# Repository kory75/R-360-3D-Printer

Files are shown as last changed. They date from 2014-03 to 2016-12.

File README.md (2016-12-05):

#R-360-3D-Printer

First open source polar RepRap 3d printer

##Documentation

You can find more information and tutorials on the following links:
[Reprap Wiki](http://reprap.org/wiki/R_360)
[replicatorwarehouse.com](http://replicatorwarehouse.com/r-360-modular-printer-with-rotating-bed/)

##BOM

###Plastic Parts

| Quantity | Description |
| --- | --- |
| 1x | Centring Tool |
| 1x | Extruder Holder |
| 1x | Extruder Holder Extension(Dual head only) |
| 1x | Extruder inlet(one is enough, but we recommend to have 3) |
| 1x | Extruder large gear |
| 1x | Extruder small gear |
| 3x | Leveller |
| 1x | X-carriage |
| 1x | X-endstop-holder |
| 1x | X-end |
| 1x | X motor holder |
| 1x | Y-axes large gear |
| 1x | Y-axes small gear |
| 1x | Y-axes support cap |
| 1x | Y base |
| 1x | Y idler |
| 1x | Z-axes base |
| 1x | Z-end top |
| 1x | Z endstop holder |
| 1x | Ramps box Bottom (optional) |
| 1x | Ramps box Top (optional) |
| 1x | LCD box back (optional) |
| 1x | LCD box front (optional) | 

###Laser Cut Parts

| Quantity | Description |
| --- | --- |
| 1x | disc_full-low |
| 1x | dixc_full-top |

###Vitamins

We use allen bolts as as standard. We marked the other types when it is diviates (like Hex Head).

####Rods

| Quantity | Description |
| --- | --- |
| 1x | 200mm M8 threaded rod
| 1x | 250mm M8 threaded rod
| 1x | 280mm M5 threaded rod
| 2x | 320mm M8 smooth rod
| 2x | 380mm M10 smooth rod  

####Bolts and Nuts And Springs

| Quantity | Description |
| --- | --- |
| 8x | M8 Nut |
| 8x | M8 Washer Shake-proof |
| 5x | M8 Washer |
| 1x | M8 Nylock Nut |
| 1x | M8 70mm Hex head Bolt |
| 21x | M3 10mm Bolt |
| 15x | M3 Nuts |
| 4x | M3 Nylock Nuts |
| 18x | M3 Washer |
| 1x | M3 12mm bolt |
| 1x | M3 16mm Bolt |
| 8x | M3 20mm Bolt |
| 3x | M3 30mm Bolt |
| 1x | M3 40mm Bolt |
| 2x | M3 50mm Hex head Bolt |
| 1x | M5 Nut |

#####Extruder Bolts and Nuts

| Quantity | Description |
| --- | --- |
| 1x | M8 Nylock Nut (extruder) |
| 1x | M8 Hobbed Bolt (extruder) |
| 2x | M8 Penny washers (extruder) |
| 4x | M8 Washers (extruder) |
| 2x | M4 50mm Bolt (extruder) |
| 2x | M4 Nut (extruder) |
| 2x | M4 Washer (extruder) |
| 1x | M3 25mm Bolt (extruder) |

####Springs

| Quantity | Description |
| --- | --- |
| 4x | Bed Springs length: 13mm inner diameter: 3.15mm |
| 1x | Extruder Spring (per extruder) length: 15mm inner diameter: 4.2mm |

####Bearings

| Quantity | Description |
| --- | --- |
| 3x | 608zz |
| 3x | 623zz |
| 4x | LM8UU |
| 4x | LM10UU |

####Electronics

| Quantity | Description |
| --- | --- |
| 1x | Ramps 1.4 | 
| 1x | Arduino Mega 2560 |
| 4x | Polulu A4988 (5 for dual setup) |
| 2x | Mechanical Endstops |
| 1x | LCD Screen (optional but strongly recommended) | 
| 1x | Power Supply 12V 5A with 2.5mm round plug and local socket power cable |
| 1x | 2.5mm solderless socket |
| 1x | USB Cable | 
| 2x | 3 wire endstop cable | 
| 4x | 4 wire Motor cables |
| 1x | 2 wire Heater cartridge (per extruder) | 
| 1x | 2 wire Fan (per extruder) | 
| 1x | 2 wire Thermostate Cable (per extruder) | 
| 1x | 2 wire Electronics Cooling Fan | 

####Motors

| Quantity | Description |
| --- | --- |
| 4x | Nema 17 (4.4kg torque) shaft flattened on one side (~1mm) |

####Extruder

ActiveX or ActiveX Dual extruder

####Other

| Quantity | Description |
| --- | --- |
| 20x | Zip ties |
| 1m | Cable organiser 1cm diameter |
| 200mm | Cable organiser 2cm diameter |
| 450mm | GT2 belt |
| 1x | GT2 pulley for 5mm shaft |
| 1x | 5mm to 5mm flexible coupling |
| | 3M blue masking tape |
| 400mm | Heat-shrink inner diameter: 2.5mm |
| 1x | 12V Power Switch | 

##Developers

Kornel Farkas 

Email: admin@replicatorwarehouse.com 

Website: Replicatorwarehouse.com

##Licences

####R-360 Printer 

[R-360 is licenced under CC-BY-SA](http://creativecommons.org/licenses/by-sa/3.0/)

####Greg's Wade Licence

The included and modified extruder parts are based on Greg's Wade extruder.
Greg's Wade Extruder is licensed under the Creative Commons - GNU GPL license. 
2010 by GregFrost
Extruder based on Prusa git repo.
http://www.thingiverse.com/thing:6713

####R-360 Logo

The R-360 logo is not included! Can I have your cool logo on my printer? :) 
R-360 Logo contains our company logo which is trade marked so please do not use unauthorised. However the logo is not required for the functionality of the printer, but it makes it look much cooler! ;) If you like to have the full experience and you would like to have our official logo on your printer :) and you would like to support us to continue to develop the R-360 printer, then please donate 5 USD to us and we will allow you to print and use our logo on your printer. :) Drop us an email to admin@replicatorwarehouse.com

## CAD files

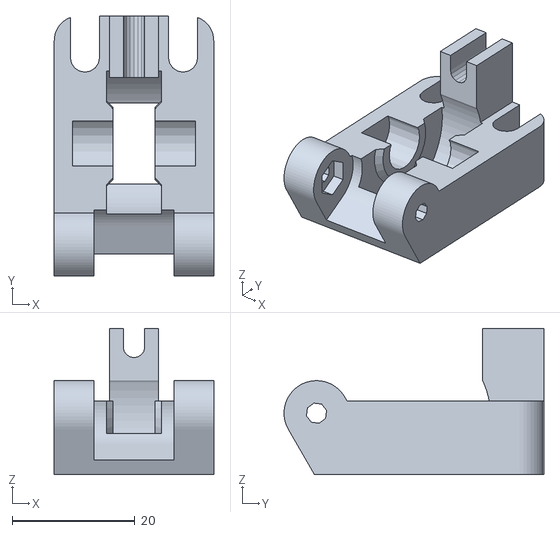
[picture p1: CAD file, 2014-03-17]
extruder/extruder_idler.stl
26.0 x 42.4 x 23.8

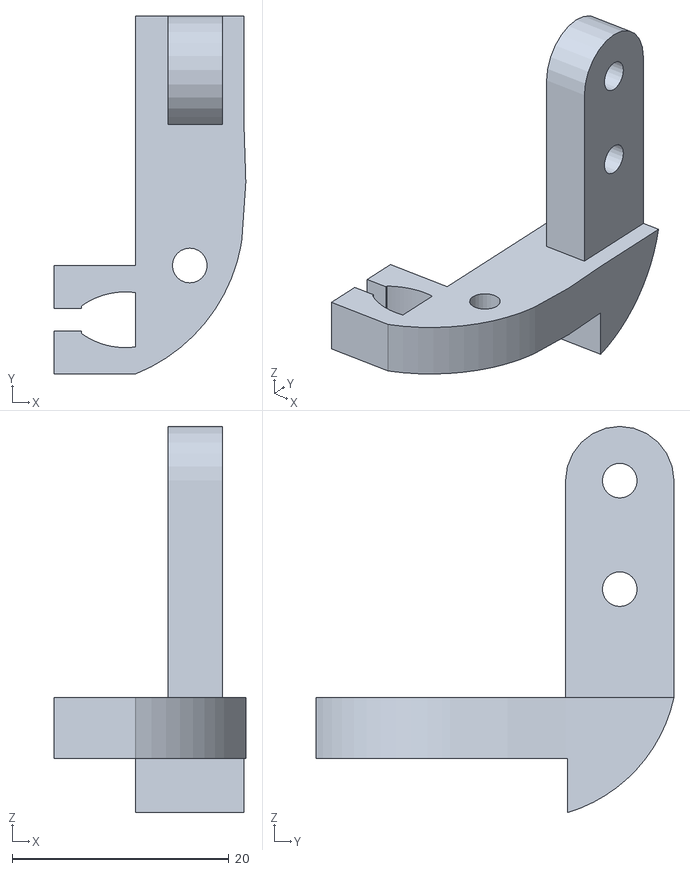
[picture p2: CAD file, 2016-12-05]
X-endstop-holder.stl
17.7 x 33.0 x 35.6

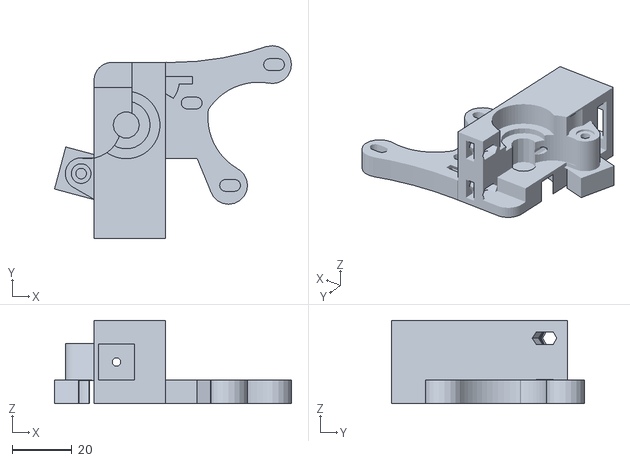
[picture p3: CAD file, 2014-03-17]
extruder/extruder body.stl
79.5 x 64.6 x 28.0

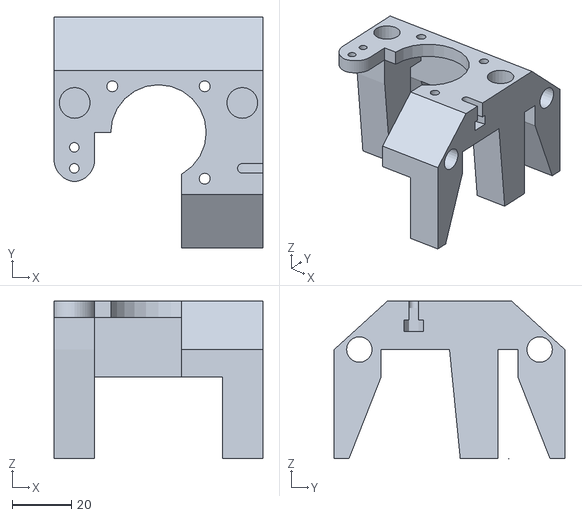
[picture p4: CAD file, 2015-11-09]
Z-axes base.stl
70.6 x 77.9 x 53.3

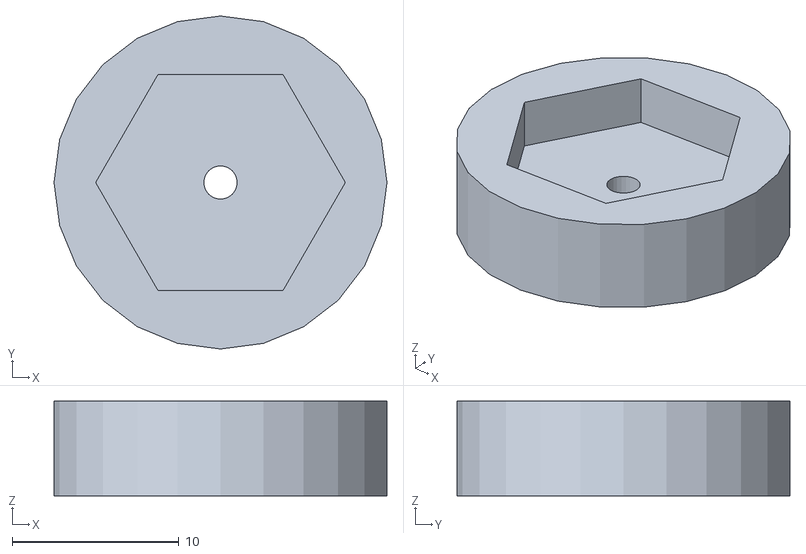
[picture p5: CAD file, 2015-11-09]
Y-axes Support cap.stl
20.0 x 20.0 x 5.70

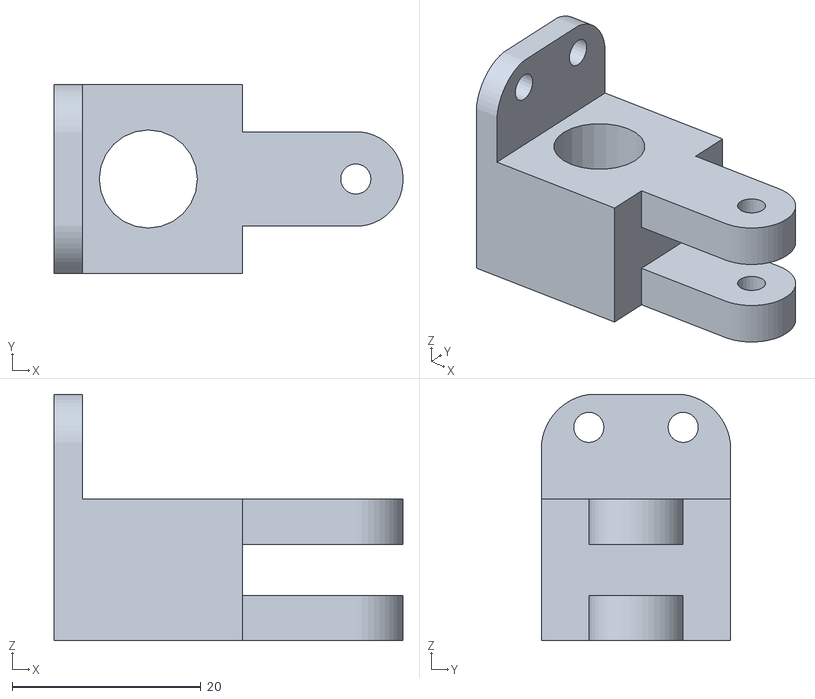
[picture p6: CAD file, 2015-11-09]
Z-endstop holder.stl
37.0 x 20.0 x 26.1

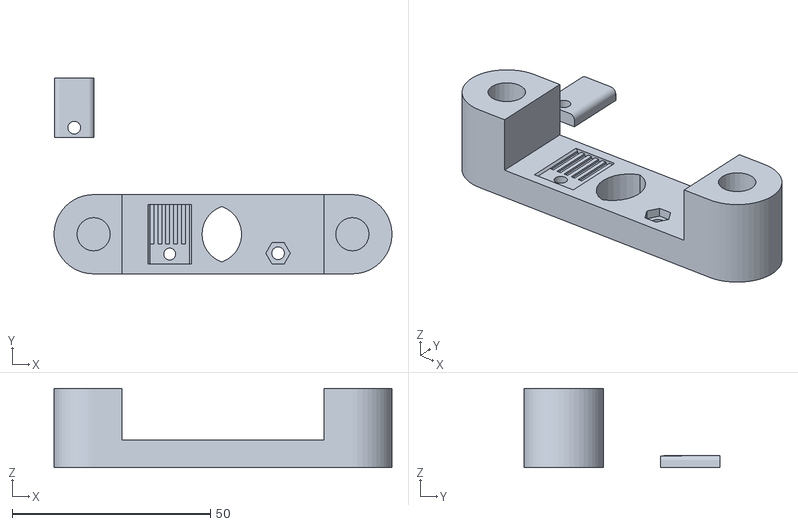
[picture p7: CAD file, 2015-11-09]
X-end.stl
85.3 x 49.4 x 20.0

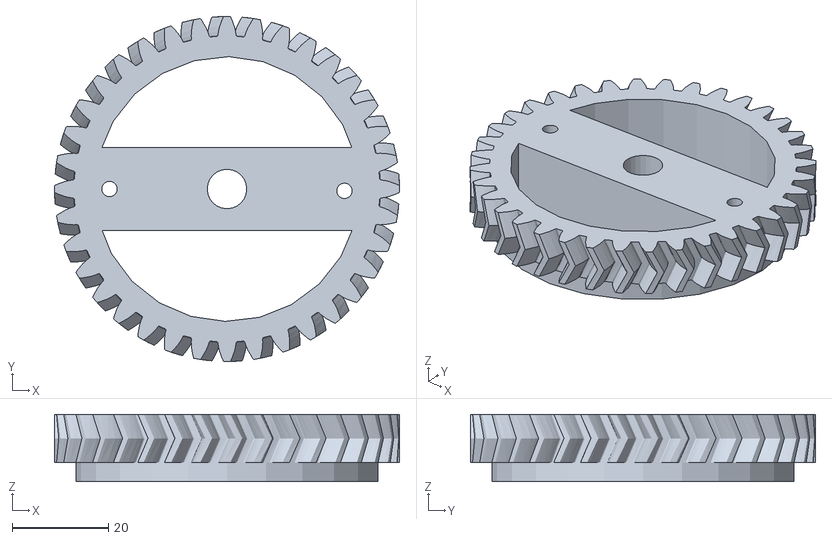
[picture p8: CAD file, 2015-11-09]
Y-axes large gear.stl
71.7 x 71.7 x 14.0

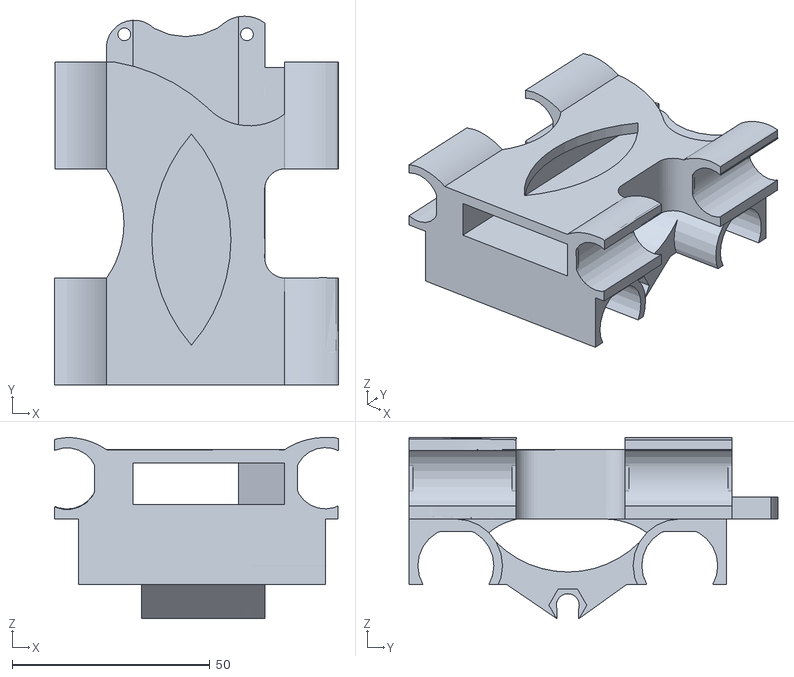
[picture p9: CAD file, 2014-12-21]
X-motor holder.stl
71.8 x 93.2 x 45.8

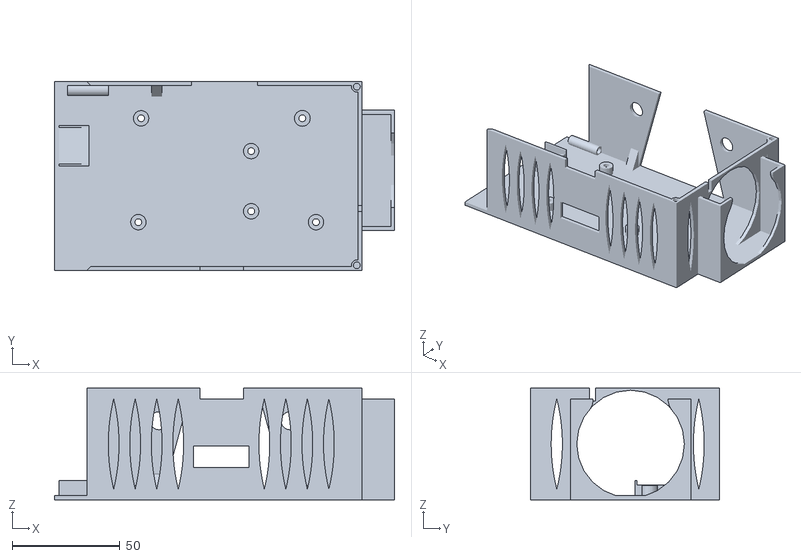
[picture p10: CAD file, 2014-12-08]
Ramps box bottom.stl
158.0 x 88.0 x 52.0

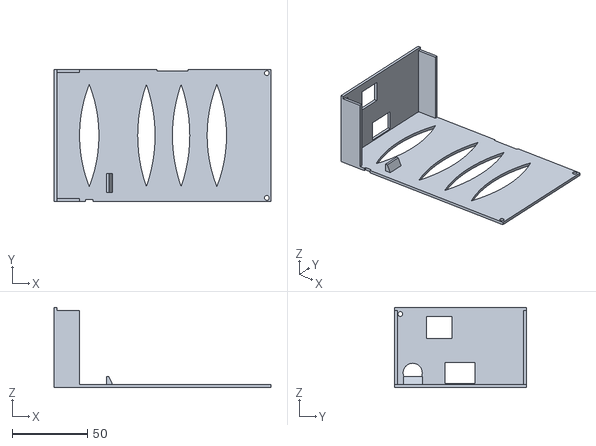
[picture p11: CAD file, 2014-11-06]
Ramps box top.stl
144.3 x 88.0 x 53.5

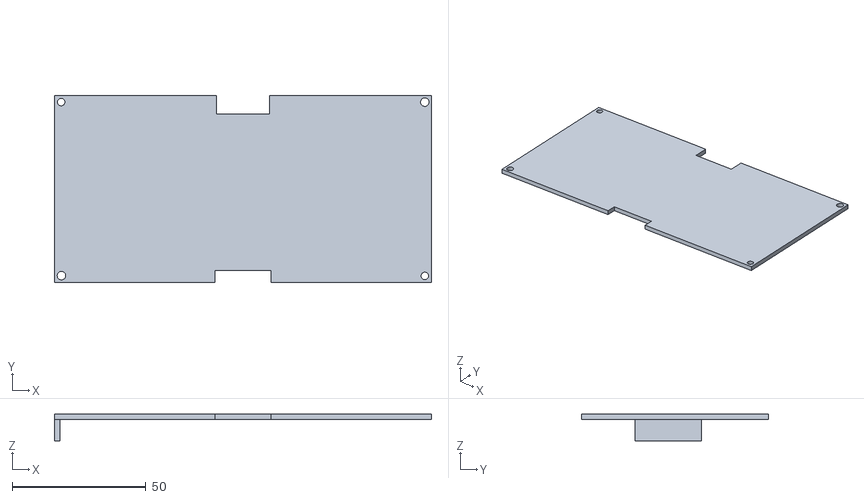
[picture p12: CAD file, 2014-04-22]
LCD box back.stl
141.0 x 70.0 x 10.0

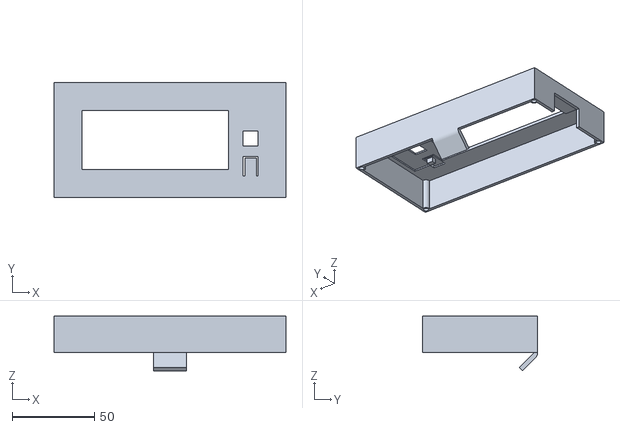
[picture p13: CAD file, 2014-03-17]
LCD box front.stl
141.0 x 70.0 x 33.2

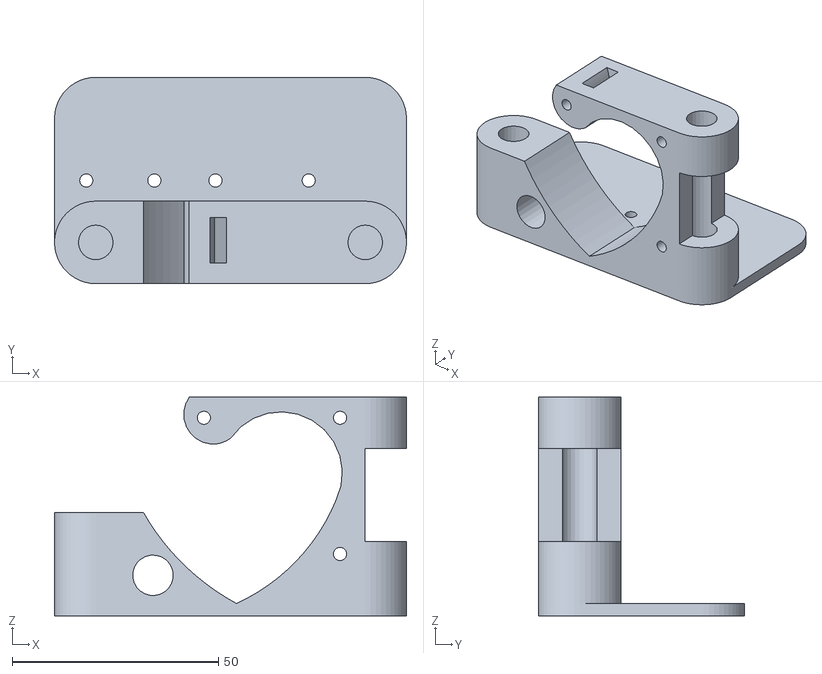
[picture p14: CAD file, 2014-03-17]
X-carriage.stl
85.3 x 50.0 x 53.0

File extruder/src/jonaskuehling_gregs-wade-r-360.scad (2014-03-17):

// Greg's Wade Extruder. 
// It is licensed under the Creative Commons - GNU GPL license. 
//  2010 by GregFrost
// Extruder based on prusa git repo.
// http://www.thingiverse.com/thing:6713

include<configuration.scad>
include<jonaskuehling-default.scad>

// Define the hotend_mounting style you want by specifying hotend_mount=style1+style2 etc.
malcolm_hotend_mount=1;
groovemount=2;
peek_reprapsource_mount=4;
arcol_mount=8;
mendel_parts_v6_mount=16; 
grrf_peek_mount=32;
wildseyed_mount=64;
geared_extruder_nozzle=128; // http://reprap.org/wiki/Geared_extruder_nozzle
jhead_mount=256;
reprapfaborg_mount=512; // http://reprap-fab.org hotend with 10mm PEEK insulator
r360=1024;


//Set the hotend_mount to the sum of the hotends that you want the extruder to support:
//e.g. wade(hotend_mount=groovemount+peek_reprapsource_mount);

//Set motor- and bolt-elevation for additional clearance when using e.g. 9/47 gears like in http://www.thingiverse.com/thing:11152
elevation=4;

//Set extra gear separation when using slightly bigger non-standard gears like 9/47 herringbone gears
extra_gear_separation=2;

// Nut wrench sizes ISO 4032
m3_wrench = 5.5;
m4_wrench = 7;

// Adjust for deeper groove in hobbed bolt, so that idler is still vertical when tightened
// Values like 0.5 to 1 should work, the more, the closer the idler will move to the bolt
// Sometimes the idler will be slightly angled towards the bolt which causes the idler screws
// to slip off the slots in die idler to the top.. Adjusting this should help:
less_idler_bolt_dist = 0;





////////// RENDER EXTRUDER //////////////////////////////////////////////////////////////
//wade(hotend_mount=groovemount, legacy_mount=false);
//wade(hotend_mount=reprapfaborg_mount, legacy_mount=false);
//wade(hotend_mount=jhead_mount, legacy_mount=false);
//wade(hotend_mount=arcol_mount, legacy_mount=false);
wade(hotend_mount=r360, legacy_mount=false);


////////// RENDER BEARING WASHER ///////////////////////////////////////////////////
//translate([-15,45,0])								// POSITIONING
//	bearing_washer();


////////// RENDER IDLER /////////////////////////////////////////////////////////////////////
//translate([78+extra_gear_separation,-10,16.20])		// POSITIONING
//	rotate([0,-90,0])
//		wadeidler();






/**
 * Extruder
 * @name Extruder
 * @assembled
 * @using 1 small-gear
 * @id extruder
 * @using 1 idler
 * @using 1 extruder-body
 * @using 1 m3nut
 * @using 1 m3washer
 * @using 1 m3x25
 * @step Take idler and insert nut into small nut-trap inside the hinge.
 * @step While holding the nut in place, preprare M3x25 bolt with washer and screw it into the hinge just enough to hold the nut.
 * @step Now take the extruder body and idler. Place idler on the hinge counterpart and compleately screw the M3x25 bolt. This will create secured hinge.
 * 
 * @using 2 m4nut
 * @step Place M4 nuts into their nut traps, secure them with piece of tape. We need them in place, since later they would be harder to access.
 * 
 * @using 3 m3x10
 * @using 3 m3washer
 * @using 1 NEMA17
 * @step Prepare your NEMA17 stepper motor and three M3x10 screws with washers.
 * @step Hold motor on place and lightly tighten the screws. We need to adjust motor position later, no need to tighten it hard.
 * 
 * @using 1 large-gear
 * @using 1 m8washer
 * @using 2 m8nut
 * @using 2 bearing-608
 * @step Place two skate bearings on ther position, they should snuggly fit in.
 * @step Insert prepared large gear into the body with mounted bearings.
 * @step Check if the alignment of hobbed part with the filament path. Adjust it accordingly with adding or removing M8 washers.
 * @step After adjusting, we need to fix the bolt in. So we place washer at the end of hobbed bolt and with two M8 nuts we will do locknut by tightening them against each other.
 * @step Check if large gear turns freely.
 * 
 * @using 2 m3x40
 * @using 4 m3washer
 * @using 2 extruder-spring
 * @step Prepare two M3x40 screws with sandwitch of washer-spring-washer.
 * @step Insert two M3 nuts into nut traps on top of drive mechanism. [[extruder/top-nut-traps.png]]
 * @step Insert prepared screws into the holes on idler. Close the idler and tighten the screws into the trapped nuts. More you tighten those screws, more pressure will be on fillament.
 * @step Your extruder is done. [[extruder/assembled.jpg]]
 */

/**
 * Extruder body
 * @name Extruder body
 * @category Printed
 * @id extruder-body
 */

/**
 * Extruder idler
 * @name Extruder Idler
 * @id idler
 * @category Printed
 * @using 1 bearing-608
 * @using 1 idler-m8-piece
 * @step Insert piece of M8 rod into bearing.
 * @step Insert 608 bearing with rod into printed idler part.
 */

/**
 * Small M8 rod 
 * @name Idler
 * @id idler-m8-piece
 * @category Rods and Bars
 */

/**
 * Spring used for idler on extruder.
 * @name Extruder spring
 * @id extruder-spring
 */

//===================================================
// Parameters defining the wade body:
wade_block_height=55+elevation;
wade_block_width=24;
wade_block_depth=28;

block_bevel_r=6;

base_thickness=7;
base_length=70;
base_leadout=25;

nema17_hole_spacing=1.2*25.4; 
nema17_width=1.7*25.4;
nema17_support_d=nema17_width-nema17_hole_spacing;

screw_head_recess_diameter=7.2;
screw_head_recess_depth=3;

motor_mount_rotation=25;
motor_mount_translation=[50.5+extra_gear_separation,34+elevation,0];
motor_mount_thickness=8;

m8_clearance_hole=8.8;
hole_for_608=22.6;
608_diameter=22;

block_top_right=[wade_block_width,wade_block_height];

layer_thickness=0.25;
filament_feed_hole_d=3;
filament_diameter=1.75;
filament_feed_hole_offset=filament_diameter+1.5;
idler_nut_trap_depth=7.3;
idler_nut_thickness=3.7;

gear_separation=7.4444+32.0111+0.25+extra_gear_separation;

function motor_hole(hole)=[motor_mount_translation[0],motor_mount_translation[1]] +
	rotated(45+motor_mount_rotation+hole*90)*nema17_hole_spacing/sqrt(2);

// Parameters defining the idler.

filament_pinch=[
	motor_mount_translation[0]-gear_separation-filament_feed_hole_offset-filament_diameter/2,
	motor_mount_translation[1],
	wade_block_depth/2];
idler_axis=filament_pinch-[608_diameter/2,0,0];
idler_fulcrum_offset=608_diameter/2+3.5+m3_diameter/2;
idler_fulcrum=idler_axis-[0+less_idler_bolt_dist,idler_fulcrum_offset,0];
idler_corners_radius=4; 
idler_height=12;
idler_608_diameter=608_diameter+2;
idler_608_height=9;
idler_mounting_hole_across=8;
idler_mounting_hole_up=15;
idler_short_side=wade_block_depth-2;
idler_hinge_r=m3_diameter/2+3.5;
idler_hinge_width=6.5;
idler_end_length=(idler_height-2)+5;
idler_mounting_hole_diameter=m4_diameter+0.25;
idler_mounting_hole_elongation=0.9;
idler_long_top=idler_mounting_hole_up+idler_mounting_hole_diameter/2+idler_mounting_hole_elongation+2.5;
idler_long_bottom=idler_fulcrum_offset;
idler_long_side=idler_long_top+idler_long_bottom;

module bearing_washer(){
	difference(){
		cylinder(r=hole_for_608/2-0.3,h=1);
		translate([0,0,-1])
		cylinder(r=8,h=3);
	}
}

module wade (hotend_mount=0,legacy_mount=false){
	difference (){
		union(){
			// The wade block.
			cube([wade_block_width,wade_block_height,wade_block_depth]);

			// Filler between wade block and motor mount.
			translate([10,motor_mount_translation[1]-hole_for_608/2,0])
			cube([wade_block_width+extra_gear_separation,
				wade_block_height-motor_mount_translation[1]+hole_for_608/2,
				motor_mount_thickness]);

			// Connect block to top of motor mount.
			linear_extrude(height=motor_mount_thickness)
			barbell(block_top_right-[0,5],motor_hole(0),5,nema17_support_d/2,100,60);

			//Connect motor mount to base.
			//linear_extrude(height=motor_mount_thickness)
			//barbell([base_length-base_leadout,
			//	base_thickness/2],motor_hole(2),base_thickness/2,
			//	nema17_support_d/2,100,60);

			// Round the ends of the base
			//translate([base_length-base_leadout,base_thickness/2,0])
			//cylinder(r=base_thickness/2,h=wade_block_depth,$fn=20);

			//translate([-base_leadout,base_thickness/2,0])
			//cylinder(r=base_thickness/2,h=wade_block_depth,$fn=20);

			//Provide the bevel betweeen the base and the wade block.
			render()
			/*difference(){
				translate([-block_bevel_r,0,0])
				cube([block_bevel_r*2+wade_block_width,
					base_thickness+block_bevel_r,wade_block_depth]);				
				translate([-block_bevel_r,block_bevel_r+base_thickness])
				cylinder(r=block_bevel_r,h=wade_block_depth,$fn=60);
				translate([wade_block_width+block_bevel_r,
					block_bevel_r+base_thickness])
				cylinder(r=block_bevel_r,h=wade_block_depth,$fn=60);
			}
*/
			// The idler hinge.
			translate(idler_fulcrum){
				translate([idler_hinge_r,0,0])
				cube([idler_hinge_r*2,idler_hinge_r*2,idler_short_side-2*idler_hinge_width-0.5],
					center=true);
				rotate(-30){
					cylinder(r=idler_hinge_r,
						h=idler_short_side-2*idler_hinge_width-0.5,
						center=true,$fn=60);
					translate([idler_hinge_r,0,0])
					cube([idler_hinge_r*2,idler_hinge_r*2,
						idler_short_side-2*idler_hinge_width-0.5],
						center=true);
				}
			}
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

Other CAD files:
printing bed/disc_full-low.dwg
printing bed/disc_full-top.dwg
Z-end top.stl
Extruder holder extension.stl
extruder/src/configuration.scad
extruder/src/functions.scad
extruder/src/gregs-wadebits.scad
Centring Tool.stl
Extruder holder.stl
Extruder inlet.stl
Extruder large gear.stl
Extruder small gear.stl
Leveler.stl
Y-Base.stl
Y-axes small gear.stl
Y-idler.stl
extruder/src/jonaskuehling-default.scad
extruder/src/metric.scad
src/Centring tool.skp
src/Extruder gears.skp
src/Extruder holder extension.skp
src/Extruder holder.skp
src/Extruder inlet.skp
src/LCD box.skp
src/Leveler.skp
src/Ramps box.skp
src/X-carriage.skp
src/X-end.skp
src/X-motor holder.skp
src/Y-Base.skp
src/Y-axes Support cap.skp
src/Y-axes large gear.skp
src/Y-axes small gear.skp
src/Y-idler.skp
src/Z-axes base.skp
src/Z-end top.skp
src/Z-endstop holder.skp
src/x-endstop-holder.skp

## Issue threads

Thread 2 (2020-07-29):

Marlin R-360

shadinew, 2020-07-29:
I have designed new 3D printer and found that Marlin R-360 is the closest to my design however when i enable #define R-360 the Y axis is not moving

the link has the design and the problem i face

https://reprap.org/forum/read.php?185,874711,875634#msg-875634

the help to resolve the issue is really appreciated

Regards;

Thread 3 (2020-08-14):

Y Axis that supposed to move the bed Theta angel is not moving

shadinew, 2020-08-14:
Hi I have the below issue , which i am not sure if it is the reason why Y axis is not moving in my machine

echo: Free Memory: 4324  PlannerBufferBytes: 1232
echo:Hardcoded Default Settings Loaded
echo:SD init fail

I have defined the R-360 however Y axis is not moving not homing too its like powerless even though i saw the coordinates are fine on the LCD but it seems in some way the coordinates are not reaching the stepper motor i changed the driver I changed the wires and flipping them with x axis which moving and not working too.

shadinew, 2020-08-14:
I use motherboard 35 and below is the code

// Enable  R_360 Polar cordinates
#define R_360
//#define R_360_MENU

//disc outer size
#define R_360_OUTER_RADIUS 100

// Make delta curves from many straight lines (linear interpolation).
// This is a trade-off between visible corners (not enough segments)
// and processor overload (too many expensive atan2 calls).
#define R_360_DELTA_SEGMENTS_PER_SECOND 250 //normal 250

//The original formula to calculate this number:
//(large gear teeth count /  small gear teeth count) / ( 360 / motor step degree * motor step ratio {1/x} ) / 2
//(36 / 10) (360 / 1.8 *16 ) /2 = 5760
//steps for full rotation -5760 to 5760 //TODO Use the full rotation here not half
//This value overide the Y settings in DEFAULT_AXIS_STEPS_PER_UNIT
#define R_360_STEPS_PER_ROTATION 5760

//Speed up in the middle. It helps if there is too much fillamet get deposited to the center of the printing bed
//Will make a quick move when larger than alpha condition(tn) and smaller than x_diff condition(mm)
//#define R_360_QUICK_CROSSING_ON
//#define R_360_ALPHA_CONDITION 0.03
//#define R_360_X_DIFF_CONDITION 2

//Choose only one
//Method 1 uses angles for detecting shorter paths. Arduino MEGA can't handle more than 5 digit accuracy with floats. Accuracy problems can couse skipping and twisted prints.(prepare_move)
//#define R_360_SHORTER_WAY_DETECTION_METHOD_1
//Method 2 Works with steps and integers. (plan_buffer_line)
//#define R_360_SHORTER_WAY_DETECTION_METHOD_2

I would like to mention that i set temps to 0 as i do not have extruder yet so i can test the movement could it be a reason ?

kory75, 2020-08-14:
Hi,

To be honest R-360 code is very-very old.

Y axis homing was disabled as Y axis were the printing plate which is a disk / circle has no zero point to home to. It did not matter where we start to print from anyway.

You need to select one of the methods to calculate coordinates:

#define R_360_SHORTER_WAY_DETECTION_METHOD_1
or
#define R_360_SHORTER_WAY_DETECTION_METHOD_2

I recommend the 2nd one (it had less accuracy issues)

Kind regards,

--
Kornel Farkas
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

shadinew, 2020-08-14:
I appreciate your reply , however it seems not working too, would it be possible to recommend any other firmware the can run a polar 3d printer with the following design ?
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

shadinew, 2020-08-14:
I used Arduino Mega and Ramps 1.4

airfield20, 2020-09-02:
@shadinew https://duet3d.dozuki.com/Wiki/ConfiguringRepRapFirmwarePolarPrinter

shadinew, 2021-04-24:
@airfield20 I have used reprapfirmware with M669 K7 however I am still facing the same issue , is there anyway you can help me in the configurations ?

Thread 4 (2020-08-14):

polar printer firmware

shadinew, 2020-08-14:
I appreciate your reply , however it seems not working too, would it be possible to recommend any other firmware the can run a polar 3d printer with the following design ?
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

shadinew, 2020-08-14:
i appreciate that you replied to previous issue #3 however can you advise me the possible firmware for the design in the pic plz and if Arduino mega will work for this design ?

kory75, 2020-08-17:
Hi,

That looks very different from an R-360. :) It is an Interesting design.
I’m not sure about other firmwares.
Is the motor has enough power to rotate all that? maybe you need to crank up the power?

Kind regards,

--
Kornel Farkas
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

shadinew, 2020-08-17:
Yes Actually i know it is a bit different however from my point of view the R-360 should work and it runs it however the drawing is not what it is supposed to be  know this machine in our to work it need R and Theta as angel. which seems available in the R-360 however my problem now is not moving the Axis is to get the outcome that matches the printed object, will be something that you can help me with my Idea of programming is coming back to 13 years ago, so if you think this is something you can help i will highly appreciate that, I consider to move Z by 2 options by small hydraulic pump or by specific design that will utilize the stepper motor movement in case i was not able to move it by pump through springs

shadinew, 2020-08-17:
equations are R=sqrt(sq(X)+sqrt(Y))
                       Theta = atan2(x,y)/1.8         // as of now I assumed the stepper will need 200 step to move 360 degrees and by that each step to generate 1.8 degrees which i assume to be reduced later to give higher accuracy .
let me know if it is something you like to work at , I feel marlin R-360 is perfect if I managed to tweak it from code perspective.

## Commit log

2014-03-17 Public release version 1.0
    This is the first release of R-360 3D printer
    [Centring Tool.stl, Centring tool.skp, Extruder gears.skp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]
2014-03-20 BOM update
    BOM is not final yet.
2014-03-21 BOM update
2014-04-13 belt size update
2014-04-22 Fixed failed export
    [LCD box back.stl]
2014-11-06 Reexported Ramps box top
    I found a broken file
    [Ramps box top.stl]
2014-12-08 Repaired stl file
    [Ramps box bottom.stl]
2014-12-21 repaired still file
    [X-motor holder.stl]
2015-11-09 Reexported stl file
    [Y-axes large gear.stl]
2015-11-09 Rexported broken stls
    [X-end.stl, Y-axes Support cap.stl, Z-axes base.stl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]
2016-12-05 X end-stop holders
    Add missing X end stop holders
    [x-endstop-holder-2.1.stl, x-endstop-holder.skp]
2016-12-05 renaming files
    [X-endstop-holder.stl]
2016-12-05 Updated bolt sizes
